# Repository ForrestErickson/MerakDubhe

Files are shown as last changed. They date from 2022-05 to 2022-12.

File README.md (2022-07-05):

# MerakDubhe
A failed bench grinder becomes an equatorial mount ("turning sow's ear" into a mount)

Drawing mechanical parts in FreeCAD

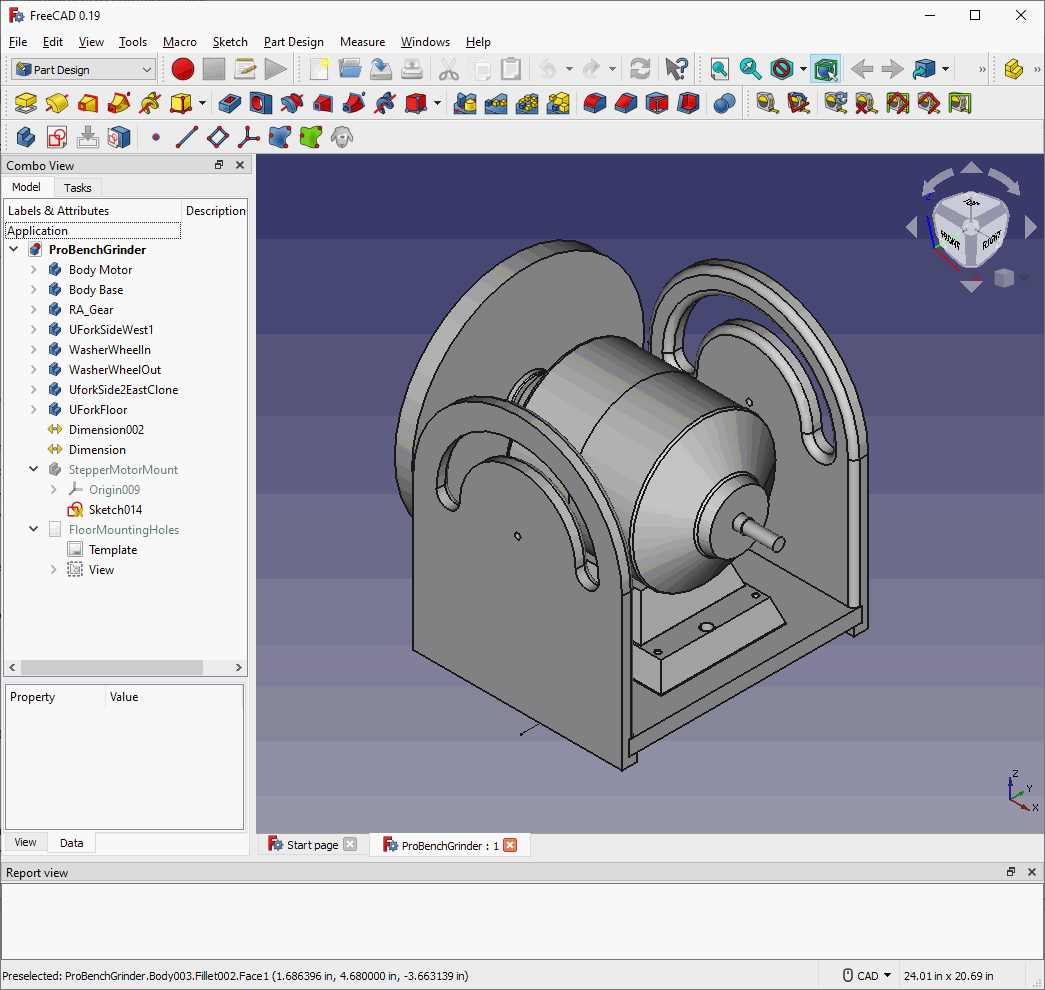
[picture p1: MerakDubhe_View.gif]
Quarter view of MerakDubhe_View


Prototype views
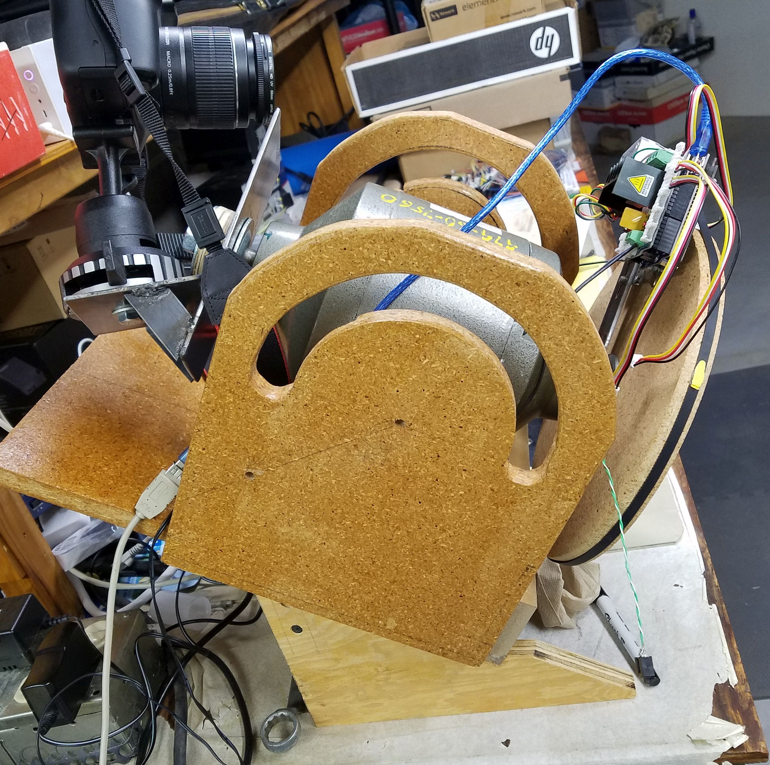
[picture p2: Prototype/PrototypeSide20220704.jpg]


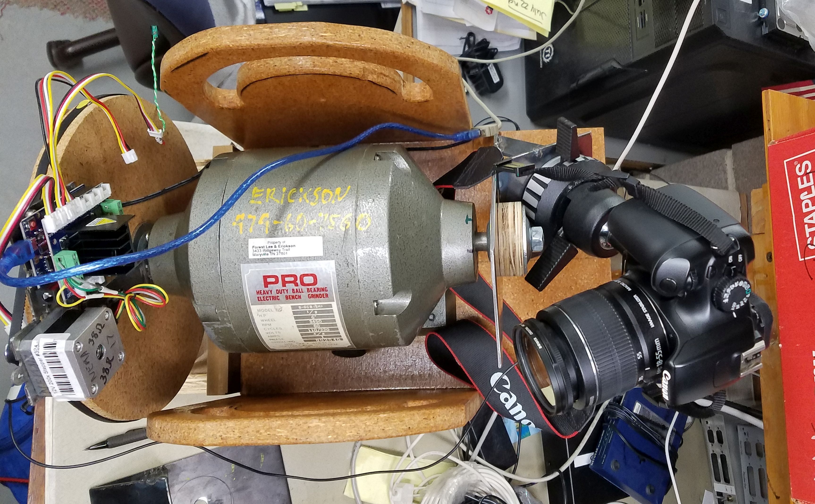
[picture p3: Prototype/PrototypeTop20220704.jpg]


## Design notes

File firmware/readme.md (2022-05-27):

# Firmware 

First version: Stepper moter control on Arduino UNO
Second version: Stepper moter controler and ESP32

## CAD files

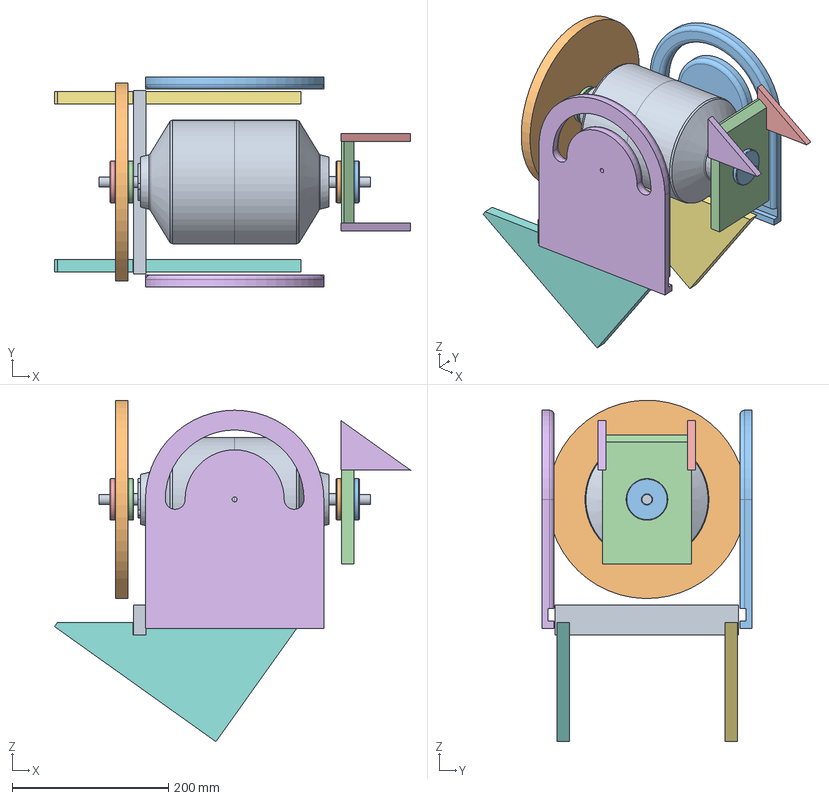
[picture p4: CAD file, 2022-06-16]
parts/ProBenchGrinder.FCStd
456.1 x 269.5 x 437.3 mm
Body Motor
RA_Gear
UForkSideWest1
WasherWheelIn
WasherWheelOut
UforkSide2EastClone
WedgeWest
WedgeEastClone
WedgeSouth
WasherCameraInside
WasherCameraOutside
CameraBracketRect
CameraSideBracketWest
CameraSideBracketEast

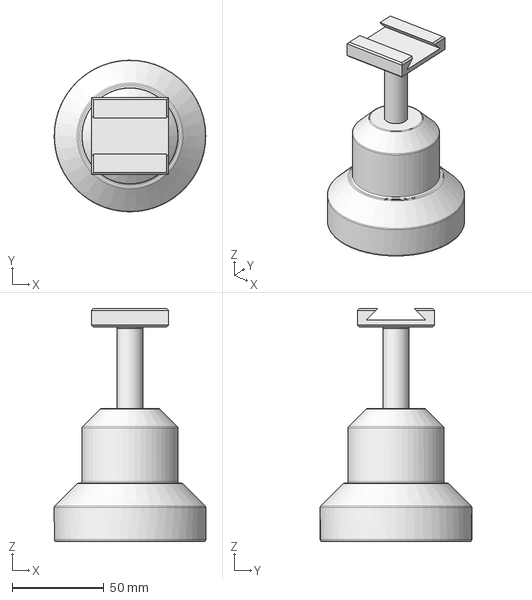
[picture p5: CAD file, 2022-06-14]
parts/PurchasedParts/BallHead3026/Bogen3026.FCStd
82.5 x 82.5 x 126.8 mm

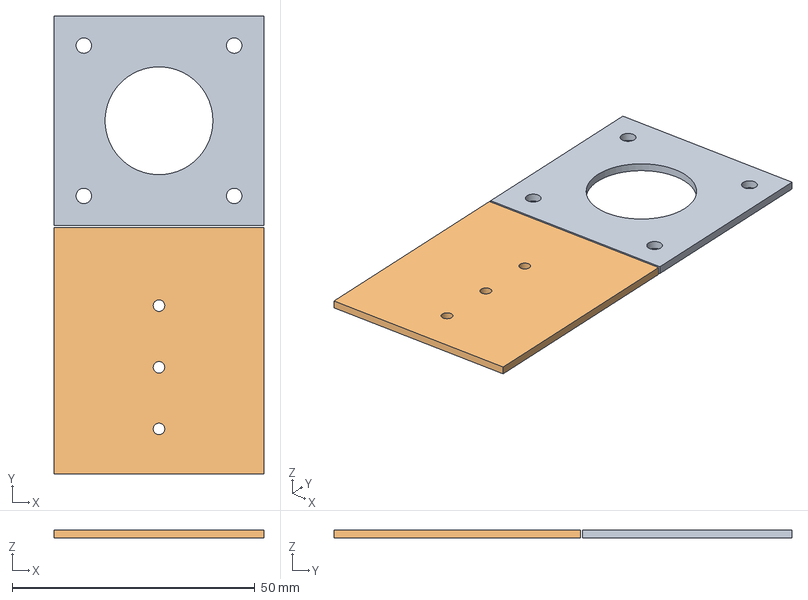
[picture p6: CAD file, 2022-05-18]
parts/NEMA17PlateMount.FCStd
43.2 x 94.4 x 1.59 mm
NEMA17PlateMount
LeverShort

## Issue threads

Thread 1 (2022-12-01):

Enhancement (Feature) Request: Add End Stop Switches

ForrestErickson, 2022-12-01:
**Is your feature request related to a problem?
Yes. The belt I fabricated with a splice does not go around the small pully well and so we should limit travel to not go around the pully. We could benifit from a start and stop travel switches.

**Describe the solution you'd like**
A clear and concise description of what you want to happen.
Switch to detect start position of Right Assension Axis
Switch to detect stop position of Right Assensation Axis.

**Describe alternatives you've considered**
A clear and concise description of any alternative solutions or features you've considered.
None.

**Additional context**
Add any other context or screenshots about the feature request here.

ForrestErickson, 2022-12-30:
End stop switches must not get broken if the RA axis has large torques.
Must either go past switch with our breakage or must have strong mechanical stop protecting switch.

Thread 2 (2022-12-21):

Enhancement (Feature) Request: Improve User Interface with Display

ForrestErickson, 2022-12-21:
**Is your feature request related to a problem? Please describe.**
A clear and concise description of what the problem is. Ex. I'm always frustrated when [...]
Improve the user experience with a display which tells the user the status of the tracking.
Trim the tracking speed.
Turn on / off guiding input.
Perhaps even let the user select other tracking speeds.

**Describe the solution you'd like**
A clear and concise description of what you want to happen.
A display and user input. The GPAD might be the display device.
A rotary encoder with push button might be the input device.

**Describe alternatives you've considered**
A clear and concise description of any alternative solutions or features you've considered.
Currently 20221221 the device has a single push button for user input which requires using either short pushes or long pushes to change device state. The device has a single LED for output to indicate state.

**Additional context**
Add any other context or screenshots about the feature request here.
Would like something powered off of the same supply as the motor and controller for simpler power supply.

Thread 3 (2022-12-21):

Enhancement (Feature) Request: Migrate to ESP32 for WiFi or BT or BLE User Interface

ForrestErickson, 2022-12-21:
**Is your feature request related to a problem? Please describe.**
_A clear and concise description of what the problem is. Ex. I'm always frustrated when [...]_
The current (20221221) user interface is very limited (one button and one LED) and I do not even remember how it works after six months of non use.

**Describe the solution you'd like**
_A clear and concise description of what you want to happen._
Change from the Arduino UNO controller to an ESP32 for wireless user interface on a smart phone.
There should be a log in for a user with full control and telemetery and an open interface for non users to observe the telemetery status only.

**Describe alternatives you've considered**
_A clear and concise description of any alternative solutions or features you've considered._
An issue has been created for an improved UI using something like the GPAD and a rotary encoder. This solution would not require a change from the Arduino UNO but has not been fully checked out.

**Additional context**
_Add any other context or screenshots about the feature request here._
None.

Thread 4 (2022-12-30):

Hardware Failure Report, Model MerakDubhe Prototype, Camera Spun Off Target, Loose RA Pully

ForrestErickson, 2022-12-30:
**Describe the Failure / Bug**
A clear and concise description of what the failure / bug is.
Short Summary of the expected behavior:  The camera should track the target.
Short Summary of the buggy behavior:  Camera mount found to have rotated away from target and was turning freely.

##  Detailed description
On about 20221227 after at least 15 minuets of tracking the target well, the system was left unattended (it was cold). After some hours the camera was found to be pointing way off target and was resting against the table on which it was mounted.
The large right ascension drive wheel was found to be loose on the shaft. The nut which secured it turned easily by hand.

**Device Under Test, aka DUT**
Steps to reproduce the behavior:
1. Model Number:   MerakDubhe
2. Serial Number(s):   Prototype.
3. Location where failure / bug occurred:  north of house in drive way.
4. Hardware configuration. (How connected, any accessories, what else it takes to replicate the system in which the failure occurred.)  The Canon T3 camera with the kit lens. Shutter release was by the MerakDubhe electrical cord.
5. Extent of Failure
** Is failure intermittent?   No it was complete.
** Is failure fixed by power cycling?  Not applicable.
** Is failure permanent?  No. Proper operation was restored by significantly tightening the nut.

**To Reproduce**
Steps to reproduce the behavior:
NA

**Expected behavior**
A clear and concise description of what you expected to happen.

**Screenshots**
If applicable, add screenshots to help explain your problem.

**Hardware description
Model:
Serial Number:
Other:

**Test Equipment
Model:
Serial Number:

**Additional context**
Add any other context about the problem here.
The nut had never been aggressively tightened.

ForrestErickson, 2022-12-30:
Torqueing both of the nuts on the RA shaft (the camera mount and the RA drive pully) to something like 10 ft-lb seams to be enough to prevent the nuts from loosening even under the load of the camera.

Closing for now.

Will have to evaluate further.

Closed 2022-12-30.

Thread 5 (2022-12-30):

The Stepper May Not Controlling of RA.

ForrestErickson, 2022-12-30:
**Describe the bug**
A clear and concise description of what the bug is.
Short Summary of the expected behavior:  When tracking, I expected the stepper motor to have control of the RA axis.
Short Summary of the buggy behavior:  During real night photography the RA axis turned unexpectedly under the weight of the camera. The tracking LED was on but the RA axis turned with little or no electronic resistance.

**To Reproduce**
Steps to reproduce the behavior:
1. It may have happened after I paused tracking with the button.

**Expected behavior**
A clear and concise description of what you expected to happen.
I expected the stepper motor to always have enough torque to hold the camera in any orientation.

**Screenshots**
If applicable, add screenshots to help explain your problem.

**Hardware description
Model: MerakDubhe
Serial Number: Prototype
Other:  Camera is Canon T3 with kit lens.

**Test Equipment
Model:  NA
Serial Number:

**Additional context**
Add any other context about the problem here.
NA

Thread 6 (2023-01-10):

Hardware Failure Report, MerakDubhe Prototype, RA Drive Wheel Came Loose On Shaft

ForrestErickson, 2023-01-10:
**Describe the Failure / Bug**
A clear and concise description of what the failure / bug is.
Short Summary of the expected behavior:
Short Summary of the buggy behavior:  During the first night under the sky after perhaps 30 minuets of exposure the camera rotated freely from the stepper.  The nut on the RA drive wheel was not tight enought to hold the axis.

**Device Under Test, aka DUT**
Steps to reproduce the behavior:
1. Model Number:   MerakDubhe
2. Serial Number(s):   Prototype
3. Location where failure / bug occurred; **RA Drive Gear retaining Nut.**
4. Hardware configuration. (How connected, any accessories, what else it takes to replicate the system in which the failure occurred.)  **Canon T3 with kit lens. The camera probably rotated free when the center of mass of the camera came across the meridian and the resulting torque overcame the nut friction. The nut was probably only finger tightned.**
5. Extent of Failure
** Is failure intermittent?  **Once loose the camera rotated down and free of furhter drive.**
** Is failure fixed by power cycling?
** Is failure permanent?

**Hardware description
Model: MerakDubhe
Serial Number: Prototype
Other:

**Test Equipment
Model: NA
Serial Number:

**Additional context**
Add any other context about the problem here.

ForrestErickson, 2023-01-10:
After the failure I torqued the nuts on both ends of the shaft to about 10 FT LB and they seam tight enough to hold the camera against torque from the camera and lens weight.

Further testing required to confirm.

ForrestErickson, 2023-01-10:
This is a duplicate of issue #4 so closing.

Closed 2023-01-10.

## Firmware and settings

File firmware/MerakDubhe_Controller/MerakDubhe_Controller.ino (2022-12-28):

/*
   MerakDubhe_Controller
   A controler for the failed bench grinder becomes an equatorial mount ("turning sow's ear" into a mount)

   Hardware includes SEEED Studio Stepper Motor Control shield Revision V1.0

   Forrest Lee Erickson
   Date: 20220529
   Released into the public domain
   Usefull reference is: https://learn.adafruit.com/diy-robotic-sky-tracking-astrophotography-mount/code

*/

/*
  Pin assignments
  A0               Auto / Serial Control  High if automatic advance.
  A1 - A5          NC

  D0  RX
  D1  TX
  D2
  D3~
  D4              Button to ground.
  D5~             Tracking_LED to power.
  D6~              /Focus    ?ring?
  D7               /Shutter  ?tip?
  D8               MOTOR CONTROL
  D9~              Output Enable Bridge A, M1
  D10~             Output Enable Bridge B, M2
  D11~             MOTOR CONTROL
  D12              MOTOR CONTROL
  D13              MOTOR CONTROL
*/

#include <DailyStruggleButton.h>
#include "CameraControl.h"

// Create an instance of DailyStruggleButton
DailyStruggleButton myButton;
extern unsigned int longPressTime;
extern byte multiHitTarget;
extern unsigned int multiHitTime;

// include the library

#include "microL298Stepper.h"   //Library made by Forrest Erickson
#define BAUDRATE 115200

#define NOT_RELEASE_MOTOR_BUTTON 4  //Use pin D4 pullup for a button to GND that will release the motor and stop tracking.

#define nTracking_LED 5 // Tracking LED from power.

/*Setup external constants */
//extern long totalMicroStepsPerRevolution;
extern const int ENA ;  //Pins for H drivers A and B enable
extern const int ENB ;
extern const int IN1 ;  // pins for IN1, IN2, IN3, IN4,
extern const int IN2 ;
extern const int IN3 ;
extern const int IN4 ;

//extern String inputString;
extern bool stringComplete;



microL298Stepper rightAssentionStepper(IN1, IN2, ENA, IN3, IN4, ENB);  //Make an object of class type microL298Stepper

unsigned long exposureCount = 0;
//bool isTimeLaps = false; //Start out not making photographs
bool isTimeLaps = true; //Start out making photographs
bool isLastExposure = false;


#include "cameracontrol.h"
WiredCamera myCanonT3(6, 7) ; //Make a camera object


bool isTracking = true; //  On 20220625 canged to true so that tracking starts at power up.
bool isNorthTracking = true; //To Do, Save setting for this in EEPROM

//Functions here
//Function to handle polarity of LED.
void TrackingLED (bool stateLED) {
  bool _stateLED = stateLED;
  if (_stateLED) {
    digitalWrite(nTracking_LED, LOW);
  } else {
    digitalWrite(nTracking_LED, HIGH);
  }//end else

}// end TrackingLED

//end functions

void setup()
{
  delay(100);
  Serial.begin(BAUDRATE);
  delay(100);

  myCanonT3.setupCameraWiredInterface();
  //  myCanonT3.printCameraPins();
  //  myCanonT3.focusAndPhoto();
  //  myCanonT3.setAutoFocus();
  //  setupCameraWiredInterface();

  //Turn on tracking LED
  digitalWrite(nTracking_LED, LOW);
  pinMode (nTracking_LED, OUTPUT);

  myButton.set(NOT_RELEASE_MOTOR_BUTTON, buttonEvent, INT_PULL_UP);
  // You can enable long press to use this feature
  myButton.enableLongPress(longPressTime);
  // You can enable multi-hit to use this feature
  myButton.enableMultiHit(multiHitTime, multiHitTarget);

  //  Serial.print("TCCR1B= "); //Print default TCCR1B
  //  Serial.println(TCCR1B);
  //  TCCR1B = TCCR1B & B11111000 | B00000011; // Set for  clkI/O/64 (From prescaler
  //Speed up PWM above audio so motor does not sing.
  TCCR1B = TCCR1B & B11111000 | B00000001; // PWM 62745.10 Hz pins 9 and 10, No prescaling,  clkI/O/1.
  //  Serial.print("TCCR1B= ");
  //  Serial.println(TCCR1B);

  // Lock the RA gear at start up.
  rightAssentionStepper.takeMicroStep(isNorthTracking); //Take a step to energize motor
  //  isTracking = false; //Then turn off tracking.
  // TrackingLED(false);

  commandMenu();
}//end setup()

void loop()
{
  myButton.poll();

  checkCommandInput();

  updateTracking();

  if (isTimeLaps) {
    isTimeLaps = myCanonT3.updateTimeLaps();
  }


  // Other code

}//end loop()

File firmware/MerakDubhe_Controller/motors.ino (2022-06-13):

/*
   motors
   Makeing the motor(s) move.
   For: MerakDubhe_Controller
   Hardware includes SEEED Studio Stepper Motor Control shield Revision V1.0

   Forrest Lee Erickson
   Date: 20220529
   Released into the public domain
*/

/*
   Stepper motor wirring notes. Facing Seeeds board wires are left to right:
   Gray, Green, Red, Yellow.
*/

#include "microL298Stepper.h"

#define stepsPerNEMA_Revolution 200  // Motor Revolution NEMA17 motor Stepper #32A
#define microSteps_PerRevolution 51200 // for this NEMA17 shaft = 200*256
#define RA_GEER_to_NEMA_GEER 20   //Gears of MerakDubhe, about 10 Inch over 1/2 inch. 
#define stepsPerShaftRevolution 4000// = stepsPerNEMA_Revolution * RA_GEER_to_NEMA_GEER; // 200*20=4000 Steps per RA gear revolution
#define totalMicroStepsPerRevolution 1024000 // = 200*256L*20; // 200*256*20 = 1024000 microSteps per RA gear revolution

//float secondsPerSideralDay = 86164.1F;
//unsigned long mSecondsPerSideralDay = secondsPerSideralDay * 1000;
#define mSecondsPerSideralDay 86164100

//float microStepPeriod = mSecondsPerSideralDay/totalMicroStepsPerRevolution;// Should be 84.14462890625
float microStepPeriod = 84.14462890625;   // Should be 84.14462890625
float nextSideralStep = 0;                // Acumulate sideral time for steps.

void updateTracking() {
  if (isTracking) {
    if (millis() > nextSideralStep) {
      //Make a step, Set next step time
      rightAssentionStepper.takeMicroStep(isNorthTracking);
      nextSideralStep = nextSideralStep + microStepPeriod;
    }//end next step
  }//end is tracking


}//end updateTracking


//void printMotorAndGear() {
//  Serial.print("System stepsPerNEMA_Revolution: ");
//  Serial.println(stepsPerNEMA_Revolution);
//  Serial.print("System microSteps_PerRevolution: ");
//  Serial.println(microSteps_PerRevolution);
//  Serial.print("System RA_GEER_to_NEMA_GEER: ");
//  Serial.println(RA_GEER_to_NEMA_GEER);
//  Serial.print("System stepsPerShaftRevolution: ");
//  Serial.println(stepsPerShaftRevolution);
//  Serial.print("System totalMicroStepsPerRevolution: ");
//  Serial.println(totalMicroStepsPerRevolution);
//  Serial.print("System mSecondsPerSideralDay: ");
//  Serial.println(mSecondsPerSideralDay);
//  Serial.print("System microStepPeriod: ");
//  Serial.println(microStepPeriod, 6);
//
//}// end printMotorAndGear

// Define some steppers and the pins they will use for Seeeds Studio Motor Shield V1.0
const int ENA = 9;  //Pins for H drivers A and B enable
const int ENB = 10;  //These pins can be Arduino UNO AnalogWrite pwm at 490 Hz..
// pins for IN1, IN2, IN3, IN4,
const int IN1 = 8;  //Non-pwm
const int IN2 = 11;  //pwm
const int IN3 = 12;
const int IN4 = 13;


void enableRA_Stepper() {
  pinMode(ENA, OUTPUT); //EnA
  pinMode(ENB, OUTPUT);  //EnB
  digitalWrite(ENA, HIGH);
  digitalWrite(ENB, HIGH);
}//end enableRA_Stepper()

void disableRA_Stepper() {
  //saves power
  digitalWrite(ENA, LOW);
  digitalWrite(ENB, LOW);
}//end enableRA_Stepper()


/*
  Move the motor back and forth just a bit. Attach the queen if you so desire.
  This function blocks.
  Argument is step delay in mSec.
*/
void wave(int stepDelay) {
  const  int NUMBER_OF_STEPS_WAVE = stepsPerShaftRevolution / 12;
  int _stepDelay = stepDelay;
  //Motor back and forth.
  Serial.println("clockwise");
  for (int i = 0; i < NUMBER_OF_STEPS_WAVE; i++) {
    Serial.print(i);
    rightAssentionStepper.takestep(true);
    delay(_stepDelay);
  }//end CW
  delay(100);
  Serial.println("counterclockwise");
  for (int i = 0; i < NUMBER_OF_STEPS_WAVE; i++) {
    rightAssentionStepper.takestep(false);
    Serial.print(-i);
    delay(_stepDelay);
  }//end CCW
  rightAssentionStepper.disable();    //Save power.
}//end wave()


/*
  Usint 255 micro steps
  Move the motor back and forth just a bit. Attach the queen if you so desire.
  This function blocks.
  Argument is step delay in mSec.
*/
void microWave(int stepDelay) {
  //  const  int NUMBER_OF_STEPS_WAVE = 1600;
  const  long NUMBER_OF_USTEPS_WAVE = totalMicroStepsPerRevolution / 12;
  int _stepDelay = stepDelay;
  Serial.println("Motor back and forth.");
  Serial.println("clockwise");
  for (int i = 0; i < NUMBER_OF_USTEPS_WAVE; i++) {
    Serial.print(i);
    rightAssentionStepper.takeMicroStep(true);
    delay(_stepDelay);
  }//end CW
  delay(1000);
  Serial.println("counterclockwise");
  for (int i = 0; i < NUMBER_OF_USTEPS_WAVE; i++) {
    rightAssentionStepper.takeMicroStep(false);
    Serial.print(-i);
    delay(_stepDelay);
  }//end CCW
  rightAssentionStepper.disable();    //Save power.
}//end wave()

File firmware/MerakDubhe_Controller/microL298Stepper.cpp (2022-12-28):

/*
   Transformed for L298
   By Forrest Lee Erickson
   Date: 20220601

   Found at: https://forum.arduino.cc/t/h-bridge-microstepping-and-only-two-pwms/461671
  microStepper4.cpp - Library for stepper motor driving
  Created by San Zamoyski, 30.05.2017
	based on
  Created by Clayton P. Webster, February 20th, 2010
  Released into the public domain
*/

#include "Arduino.h"
#include "microL298Stepper.h"

//Pin pattern:  non-pwm non-pwm pwm   non-pwm   non-pwm  pwm
microL298Stepper::microL298Stepper(int coil1a, int coil1b, int pwm1, int coil2a, int coil2b, int pwm2)
{
  digitalWrite(coil1a, LOW);
  digitalWrite(coil1b, LOW);
  digitalWrite(coil2a, LOW);
  digitalWrite(coil2b, LOW);
  pinMode(coil1a, OUTPUT);
  pinMode(coil1b, OUTPUT);
  pinMode(coil2a, OUTPUT);
  pinMode(coil2b, OUTPUT);
  _coil1a = coil1a;
  _coil1b = coil1b;
  _coil2a = coil2a;
  _coil2b = coil2b;
  _pwm1 = pwm1;
  _pwm2 = pwm2;
  _counter = 0;
}//Class decleration

long microL298Stepper::counter(){
//int microL298Stepper::counter() {
  return (_counter);
}// end counter

//int * microL298Stepper::steps1024(int count){
byte * microL298Stepper::steps1024(int count) {
  return (_steps1024(count));
}// end counter


/*Set coils on and full PWM to act as electronic break to hold against rotation*/
void microL298Stepper::hold()
{
  digitalWrite(_coil1a, _steps[_counter][0]);
  digitalWrite(_coil1b, _steps[_counter][1]);
  analogWrite(_pwm1, _steps[_counter][2]);
  digitalWrite(_coil2a, _steps[_counter][3]);
  digitalWrite(_coil2b, _steps[_counter][4]);
  analogWrite(_pwm2, _steps[_counter][5]);
}//end hold()


/*Set coils off and PWM off to save power*/
void microL298Stepper::disable()
{
  digitalWrite(_coil1a, LOW);
  digitalWrite(_coil1b, LOW);
  digitalWrite(_coil2a, LOW);
  digitalWrite(_coil2b, LOW);
  analogWrite(_pwm1, 0);
  analogWrite(_pwm2, 0);
}//end disable

/*Microsteps forward or reverse*/
void microL298Stepper::takestep(boolean invert)
{
  if (invert == false) { // CW
    _counter = _counter + 1;
    // roll over counter if they go too high
    if (_counter >= microsteps) {
      _counter = 0;
    }
  }
  else { // CCW
    _counter = _counter - 1;
    // reset counter if they go too low
    if (_counter < 0) {
      _counter = microsteps - 1;
    }
  }

  Serial.print(_counter);
  Serial.print(" => ");
  Serial.print(_steps[_counter][0]);
  Serial.print(" ");
  Serial.print(_steps[_counter][1]);
  Serial.print(" ");
  Serial.print(_steps[_counter][2]);
  Serial.print(" ");
  Serial.print(_steps[_counter][3]);
  Serial.print(" ");
  Serial.print(_steps[_counter][4]);
  Serial.print(" ");
  Serial.print(_steps[_counter][5]);
  Serial.println();

  // use digitalWrite to turn on coil, and analogWrite to create pwm for each coil
  digitalWrite(_coil1a, _steps[_counter][0]);
  digitalWrite(_coil1b, _steps[_counter][1]);
  analogWrite(_pwm1, _steps[_counter][2]);
  digitalWrite(_coil2a, _steps[_counter][3]);
  digitalWrite(_coil2b, _steps[_counter][4]);
  analogWrite(_pwm2, _steps[_counter][5]);

}//end takestep

/*takeMicroStep forward or reverse*/
// _longCounter tracks the position.
void microL298Stepper::takeMicroStep(boolean invert)
{
  byte * p ; //Pointer to byte array of aize six.
  if (invert == false) { // CW
    _counter = _counter + 1;
    // roll over counter if they go too high
    if (_counter >= microsteps1024) {
      _counter = 0;
    }
    _longCounter++;
  }
  else { // CCW
    _counter = _counter - 1;
    // reset counter if they go too low
    if (_counter < 0) {
      _counter = microsteps1024 - 1;
    }
    _longCounter--;
  }

  //  p = _steps1024(0);
  p = _steps1024(_counter);

//Print out the step status.
//  Serial.print(_counter);
//  Serial.print("  Microstep count: ");
//  Serial.println(_longCounter);

  //  Serial.print("p= ");
  //  //  Serial.print(*p);
  //  Serial.print(int(p[0]));
  //  Serial.print(", ");
  //  Serial.print(int(p[1]));
  //  Serial.print(", ");
  //  Serial.print(int(p[2]));
  //  Serial.print(", ");
  //  Serial.print(int(p[3]));
  //  Serial.print(", ");
  //  Serial.print(int(p[4]));
  //  Serial.print(", ");
  //  Serial.print(int(p[5]));
  //  Serial.println();

  digitalWrite(_coil1a, int(p[0]));
  digitalWrite(_coil1b, int(p[1]));
  analogWrite(_pwm1, int(p[2]));
  digitalWrite(_coil2a, int(p[3]));
  digitalWrite(_coil2b, int(p[4]));
  analogWrite(_pwm2, int(p[5]));



}//end takeMicroStep

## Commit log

2022-05-11 Initial commit. Profile of upper right of bench grinder horizontal dimensions only.
    [ProBenchGrinder.FCStd]
2022-05-11 Revolve profile to make right half. Mirror to make left half. Make base geometery.
    [ProBenchGrinder.FCStd]
2022-05-11 Add 10 x 0.75 inch RA gear on left.
    [ProBenchGrinder.FCStd]
2022-05-12 Add 1/4-20 holes to base. Add locating holes to base.
    [ProBenchGrinder.FCStd]
2022-05-12 Add arc hole as hand hold to UForkSide1 with inside only fillet.
    [ProBenchGrinder.FCStd]
2022-05-12 Correct sholder on shaft from 5 to 4.6 inches.
    [ProBenchGrinder.FCStd]
2022-05-13 Add washer to RA gear inner and outer.
    [ProBenchGrinder.FCStd]
2022-05-13 Used clone and translate to replace UForkSide2 with a clone of side one. I also renamed the sides to reflect west and east.
    [ProBenchGrinder.FCStd]
2022-05-18 Add a NEMA17 mounting plate idea. Start adding mounting holes to UForkFloor.
    [NEMA17PlateMount.FCStd, ProBenchGrinder.FCStd]
2022-05-19 Rework constraints on UForkSideWest1. Set board thickness from 0.75 to 0.625.to
    [ProBenchGrinder.FCStd]
2022-05-27 Add the UForkFloor to drawing.
    [ProBenchGrinder.FCStd]
2022-05-27 Make a parts folder and move drawings to same.
    [NEMA17PlateMount.FCStd, ProBenchGrinder.FCStd]
2022-05-27 Add a screen shot of the drawing for MerakDubhe equatorial mount.
2022-05-30 Add Arduino UNO controler sketch for the project. Copied from example simplty to get stepper moving.
2022-05-30 Clean up removing dead code. Make a file for motor code but not yet moved it.
2022-05-30 Move code into motor file for setup constants. Not able to created Stepper object in motor file.
2022-06-01 Add motors tab to hold stepper motor setup and functions.
2022-06-01 Rename class and class elements, Add pwm1 and pwm2 arguments to constructor. Not using the pwm yet.
2022-06-12 Use steps1024 to microstep. Does not seam to be advanceing. Stepper sings. This is working for 1Q only.
2022-06-12 Add command to turn motor one revolution with 200 takestep.
2022-06-12 Add command to turn motor one revolution with 800 quarter takesteps.
2022-06-12 Add command to turn motor one revolution with 200*256 microsteps.
2022-06-13 Define motor, step and gearing. Define step times. Freshen auto formating.
2022-06-13 Change TCCR1B to speed up pin 9, 10 PWM out of hearing.
2022-06-13 Make west wedge.
    [ProBenchGrinder.FCStd]
2022-06-14 Start Camera Mount.
    [ProBenchGrinder.FCStd]
2022-06-14 Add a crude Bogen3026 Ball Head Camera Mount.
    [Bogen3026.FCStd]
2022-06-16 Correct length of motor, center to face of guard mount. Correct shaft length.
    [ProBenchGrinder.FCStd]
2022-06-16 Reposition washers, RA gear and Camera Mount Brackets.
    [ProBenchGrinder.FCStd]
2022-06-25 Add a button that when pressed stops tracking and releases the motor so RA can be set manual.
2022-06-27 Add debouncing library and event for button management to relese and restart tracking.
2022-06-27 Add a TrackingLED. Clean up some dead code and white space. LED working. Button mostly working.
2022-06-27 Set for no track at start. Press button to start tracking. Button workes more intuivily. LED shows tracking status.
2022-07-01 Add camera control class and functions for Focus, MakePhoto and user interface for same.
2022-07-05 Make Camera Controler a class and put in .cpp and .h tabs. Start of time laps delay bug.
    [MerakDubhe_Controller.ino, SerialInteface.ino, cameracontrol.cpp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]
2022-07-05 Print exposure time in help menu.
2022-07-05 Add prototype photos.
2022-07-05 Update README.md
    Add photos of the prototype.
2022-12-28 Fix for long exposures. Several time variables changed from int to long. Some debug print statements still in this code.
    [DailyStruggle_Button.ino, MerakDubhe_Controller.ino, SerialInteface.ino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]
2022-12-28 Remove or comment debug print statements.
2022-12-28 Report exposure count. Have current exposure complete when tracking stops.
